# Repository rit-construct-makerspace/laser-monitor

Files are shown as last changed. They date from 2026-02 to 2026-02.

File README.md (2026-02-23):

# Laser Monitor 

This circuit will monitor a laser cutter's filter control and air input, and ensure both are operating properly when the laser is on. If not, warn the user.

## Setup
* Connect the fume extractor control line to the female DB9 of the laser monitor.
  * If using V1.0.**0** hardware, must invert the pinout with an adapter cable.
  * 5-1, 9-6, 4-2, 8-7, 3-3, 7-8, 2-4, 6-9, 1-5
* Connect the male DB9 on the laser monitor to the laser cutter's fume control output.
* Cut the air line to the laser cutter, and install the flex host T-joint.
* Connect 3mm ID tube to the air transducer on the PCB, and the other side to the T-joint.
* Connect 12v power supply.
* Connect laser monitor via USB to computer, open serial terminal with baud rate 115200.
* Send the following config commands;
  * Set the start delay with d [ms], i.e. "d 10000" for a 10-second startup
    * Make sure to set the same startup time in the Epilog laser
  * Set the air pressure threshold with a [val], i.e. "a 7000000"
    * Tip: use "c" to see the current air monitor reading to determine a threshold appropriate for your system.
  * Set the filter full warning with w [0/1], i..e "w 1" if you want to be warned when the filter is reporting full
    * This does not disable the fault response, just the low pressure filter warning.
  * You should be all set! Make sure to do tests on the system.

## Bill of Materials
* Assembled PCB (See Electronics Folder)
* 6x 3mm Plywood Laser Cut Case Parts (See Mechanical Folder)
* 12v >3A Barrel Jack Power Supply
* Andon Light Tower (12v) With Buzzer
  * Suggested that a blinking red light is used
  * Common anode or common cathode systems permitted, set control mode switch accordingly.
* DB9 Extension Cable (Connect Laser to Laser Monitor)
* Flex Hose T-Joint
* 3mm ID Flex Hose (OD sized to fit current system, 8mm normal)
* SparkFun 14 Segment Dispaly COM-16916 (Optional) + QWIIC to 2.54mm DuPont cable
* Threaded Rubber Magnet (1/4-20 thread)
* Hardware
  * 4x M2.5 25mm Standoffs
  * 4x M2.5 12mm Standoffs
  * 4x M2.5 6mm Spacers
  * 8x M2.5 Screw
  * 8x M2.5 Nut
  * 4x M5 Bolt
  * 4x M5 Nut

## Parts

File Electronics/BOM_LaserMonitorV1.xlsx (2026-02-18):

No. | Quantity | Comment | Designator | Footprint | Value | Manufacturer Part | Manufacturer | Supplier Part | Supplier
1 | 2 | 10uF | C1,C5 | C0603 | 10uF | CL10A106MA8NRNC | SAMSUNG(三星) | C96446 | LCSC
2 | 21 | 100nF | C2,C3,C4,C6,C7,C12,C13,C14,C15,C16,C17,C20,C21,C22,C23,C26,C27,C29,C30,C31,C32 | C0603 | 100nF | CC0603KRX7R9BB104 | YAGEO(国巨) | C14663 | LCSC
3 | 4 | 22uF | C8,C9,C10,C11 | C1206 | 22uF | CL31A226KAHNNNE | SAMSUNG(三星) | C12891 | LCSC
4 | 3 | 1uF | C18,C19,C28 | C0603 | 1uF | CL10A105KB8NNNC | SAMSUNG(三星) | C15849 | LCSC
5 | 2 | 15pF | C24,C25 | C0603 | 15pF | CL10C150JB8NNNC | SAMSUNG(三星) | C1644 | LCSC
6 | 1 | DR-9M | CN1 | DR9-TH_ZHOUR_DR-9P-R |  | DR-9M | ZHOURI(洲日) | C3020655 | LCSC
7 | 1 | DR-9F | CN2 | DR9-TH_ZHOUR_DR-9P-L |  | DR-9F | ZHOURI(洲日) | C3020657 | LCSC
8 | 1 | DB103-5.0-5P-BU-S | CN3 | CONN-TH_5P-P5.00_DB103-5.0-5P-BU-S |  | DB103-5.0-5P-BU-S | DORABO(地博电气) | C430589 | LCSC
9 | 1 | 921-111A1010D10200 | CN4 | USB-B_TH_USB-B-FEMALE-90 |  | 921-111A1010D10200 | 精拓金 | C46392 | LCSC
10 | 1 | DS1038-15FBNSiA74-0CC | CN5 | DSUB-TH_DS1038-15FBNSIA74-0CC |  | DS1038-15FBNSiA74-0CC | CONNFLY | C75754 | LCSC
11 | 5 | SS34 | D1,D2,D3,D4,D7 | SMA_L4.3-W2.6-LS5.2-RD |  | SS34 | MDD(辰达半导体) | C8678 | LCSC
12 | 4 | SRV05-4 | D5,D6,D8,D9 | SOT-23-6_L2.9-W1.6-P0.95-LS2.8-BL |  | SRV05-4 | TECH PUBLIC(台舟) | C558418 | LCSC
13 | 1 | DC-005-A250 | DC1 | DC-IN-TH_DC-005-A250 |  | DC-005-A250 | XUNPU(讯普) | C720558 | LCSC
14 | 4 | MF-NSMF050-2 | F1,F2,F3,F4 | F1206 |  | MF-NSMF050-2 | BOURNS | C75464 | LCSC
15 | 1 | HDR-M_2.54_1x4P | H1 | HDR-TH_4P-P2.54-V-M
16 | 1 | HDR-F_2.54_2x3 | H2 | HDR-TH_6P-P2.54-V-F-R2-C3-S2.54
17 | 1 | 10uH | L1 | L1206 | 10uH | CMI321609X100KT | FH(风华) | C1051 | LCSC
18 | 1 | KT-0603R | LED1 | LED0603-RD |  | KT-0603R | KENTO | C2286 | LCSC
19 | 1 | MMBT4403 | Q1 | SOT-23-3_L2.9-W1.3-P0.95-LS2.4-BR |  | MMBT4403 | R+O(宏嘉诚) | C20069140 | LCSC
20 | 1 | 20kΩ | R1 | R0603 | 20kΩ | 0603WAF2002T5E | UNI-ROYAL(厚声) | C4184 | LCSC
21 | 1 | 8.2kΩ | R2 | R0603 | 8.2kΩ | 0603WAF8201T5E | UNI-ROYAL(厚声) | C25981 | LCSC
22 | 2 | 100Ω | R3,R4 | R0603 | 100Ω | 0603WAF1000T5E | UNI-ROYAL(厚声) | C22775 | LCSC
23 | 14 | 390Ω | R5,R6,R8,R9,R11,R12,R14,R15,R17,R18,R19,R20,R29,R37 | R0805 | 390Ω | 0805W8F3900T5E | UNI-ROYAL(厚声) | C17655 | LCSC
24 | 13 | 10kΩ | R7,R10,R13,R16,R22,R23,R24,R25,R31,R32,R33,R34,R35 | R0603 | 10kΩ | 0603WAF1002T5E | UNI-ROYAL(厚声) | C25804 | LCSC
25 | 4 | 4.7kΩ | R21,R26,R27,R28 | R0603 | 4.7kΩ | 0603WAF4701T5E | UNI-ROYAL(厚声) | C23162 | LCSC
26 | 2 | 1kΩ | R30,R36 | R0603 | 1kΩ | 0603WAF1001T5E | UNI-ROYAL(厚声) | C21190 | LCSC
27 | 1 | SS-22F07-G100 | SW1 | SW-TH_6P-L16.5-W7.5-P4.0-LS2.6-TL |  | SS-22F07-G100 | G-Switch(品赞) | C5446810 | LCSC
28 | 1 | HX711 | U1 | SOP-16_L10.0-W3.9-P1.27-LS6.0-BL |  | HX711 | AVIA(海芯科技) | C6705483 | LCSC
29 | 1 | WF100SPZ 2BG D6 AT | U2 | DIP-6_L8.5-W8.5-P2.54-LS10.2-TL |  | WF100SPZ 2BG D6 AT | WF(伟烽) | C2886644 | LCSC
30 | 12 | AT172-CuH-S | U3,U4,U5,U6,U7,U8,U9,U10,U11,U12,U13,U14 | SOP-4_L4.6-W4.2-P2.54-LS7.1-BL |  | AT172-CuH-S | AOTE(奥特) | C20624244 | LCSC
31 | 4 | SN74LVC1T45DBVR | U15,U16,U17,U18 | SOT-23-6_L2.9-W1.6-P0.95-LS2.8-BR |  | SN74LVC1T45DBVR | TI(德州仪器) | C7843 | LCSC
32 | 2 | MX5052S | U19,U24 | SOP-8_L4.9-W3.9-P1.27-LS6.0-BL |  | MX5052S | Wuxi Maxinmicro(无锡明芯微) | C5875696 | LCSC
33 | 1 | DS18B20Z | U20 | SOP-8_L4.9-W3.9-P1.27-LS6.0-BL |  | DS18B20Z | UMW(友台半导体) | C695837 | LCSC
34 | 1 | L78M05ABDT-TR | U21 | TO-252-2_L6.5-W6.1-P4.58-LS10.0-TL |  | L78M05ABDT-TR | ST(意法半导体) | C58069 | LCSC
35 | 1 | ATMEGA328PB-AU | U22 | TQFP-32_L7.0-W7.0-P0.80-LS9.0-BL |  | ATMEGA328PB-AU | MICROCHIP(美国微芯) | C132230 | LCSC
36 | 1 | CH340C | U23 | SOP-16_L10.0-W3.9-P1.27-LS6.0-BL |  | CH340C | WCH(南京沁恒) | C7464026 | LCSC
37 | 1 | 16MHz | X1 | OSC-SMD_4P-L3.2-W2.5-BL | 16MHz | X322516MLB4SI | YXC(扬兴晶振) | C13738 | LCSC

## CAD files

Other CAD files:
Mechanical/Laser Monitor Assembly.f3z

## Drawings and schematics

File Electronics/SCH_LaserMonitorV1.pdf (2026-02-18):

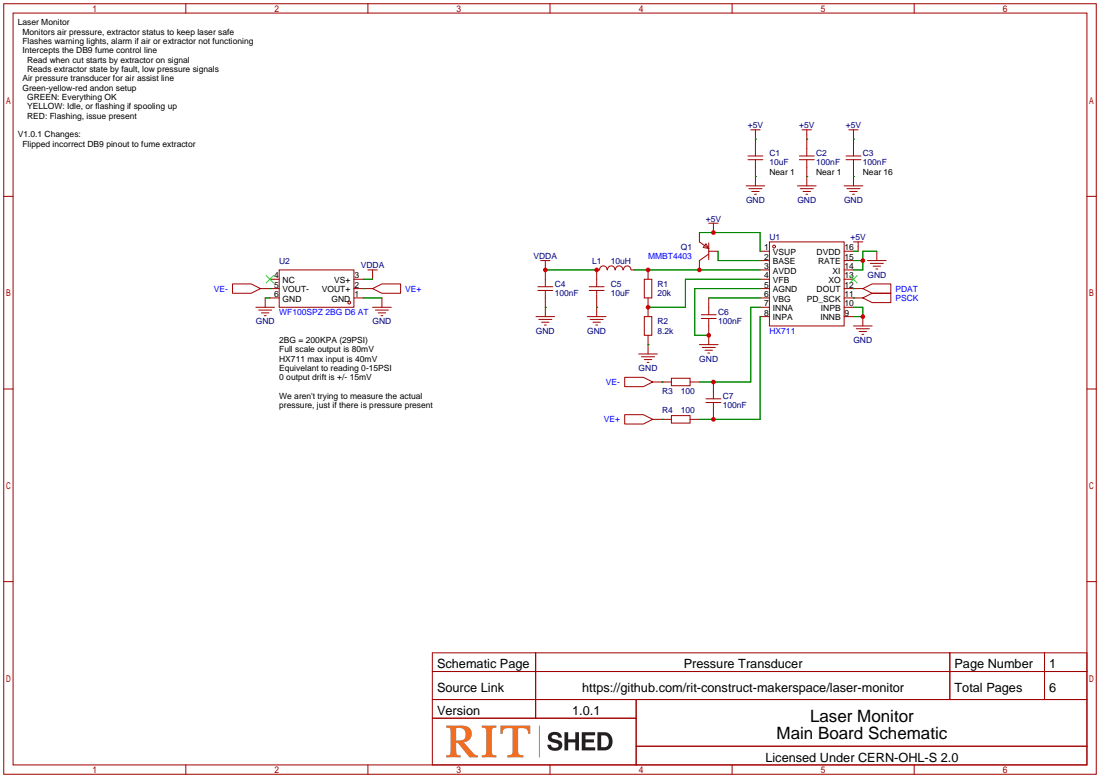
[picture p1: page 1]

Laser Monitor
Monitors air pressure, extractor status to keep laser safe
Flashes warning lights, alarm if air or extractor not functioning
Intercepts the DB9 fume control line
Read when cut starts by extractor on signal
Reads extractor state by fault, low pressure signals
Air pressure transducer for air assist line
Green-yellow-red andon setup
GREEN: Everything OK
YELLOW: Idle, or flashing if spooling up
RED: Flashing, issue present
V1.0.1 Changes:
Flipped incorrect DB9 pinout to fume extractor

INPB 10 PD_SCK 11 DOUT 12 XO 13 XI 14 RATE 15 DVDD 16

VOUT- 5
GND 6
WF100SPZ 2BG D6 AT
2BG = 200KPA (29PSI)
Full scale output is 80mV
HX711 max input is 40mV
Equivelant to reading 0-15PSI
0 output drift is +/- 15mV
We aren't trying to measure the actual
pressure, just if there is pressure present

Schematic Page | Pressure Transducer | Page Number | 1
Source Link | https://github.com/rit-construct-makerspace/laser-monitor | Total Pages | 6

Main Board Schematic

Licensed Under CERN-OHL-S 2.0

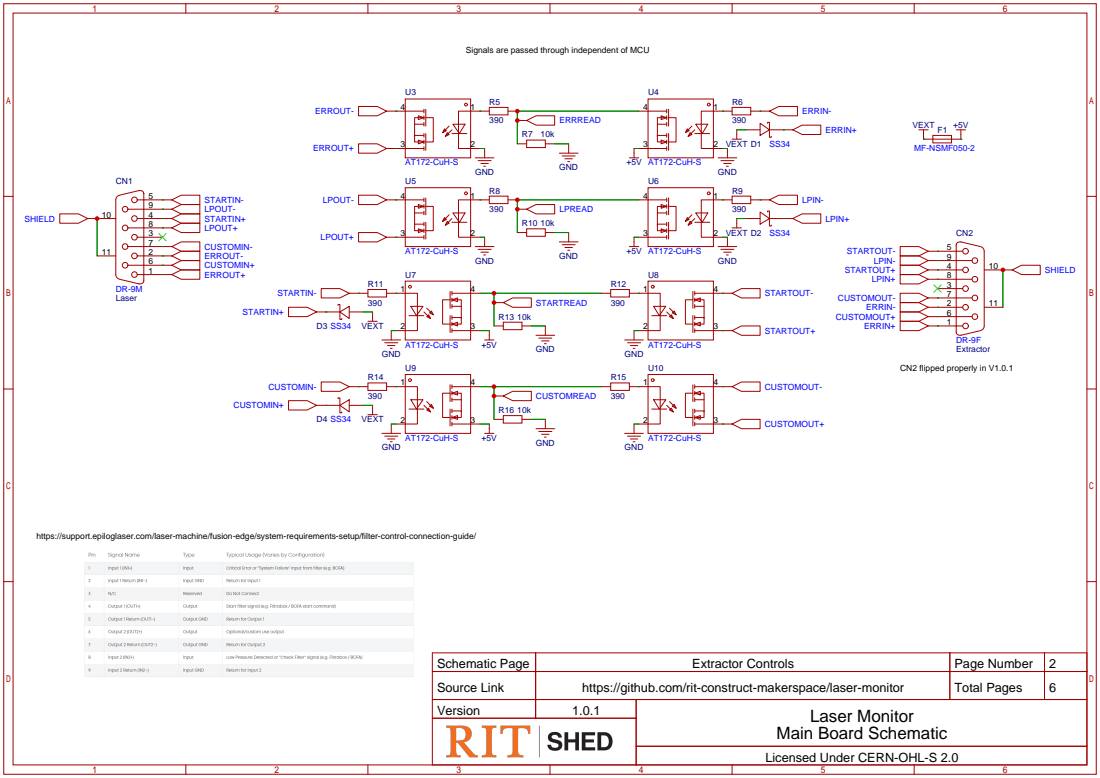
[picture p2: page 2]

Signals are passed through independent of MCU

https://support.epiloglaser.com/laser-machine/fusion-edge/system-requirements-setup/filter-control-connection-guide/

Schematic Page | Extractor Controls | Page Number | 2
Source Link | https://github.com/rit-construct-makerspace/laser-monitor | Total Pages | 6

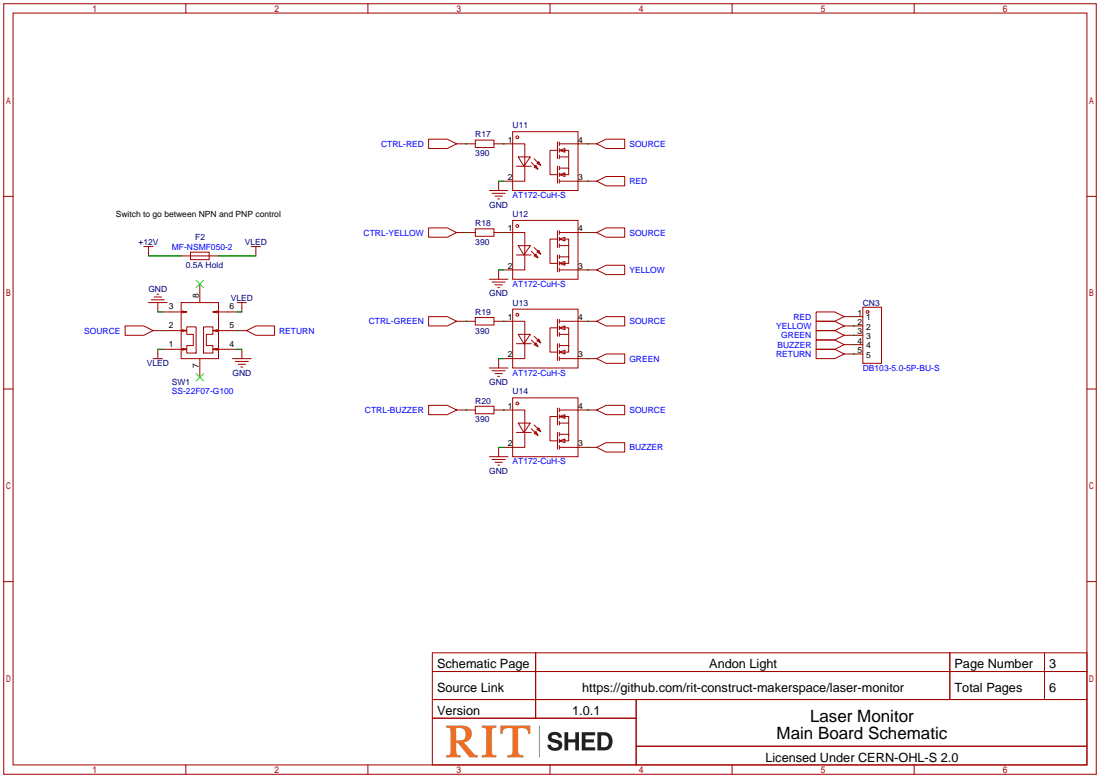
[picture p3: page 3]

Switch to go between NPN and PNP control

Schematic Page | Andon Light | Page Number | 3
Source Link | https://github.com/rit-construct-makerspace/laser-monitor | Total Pages | 6

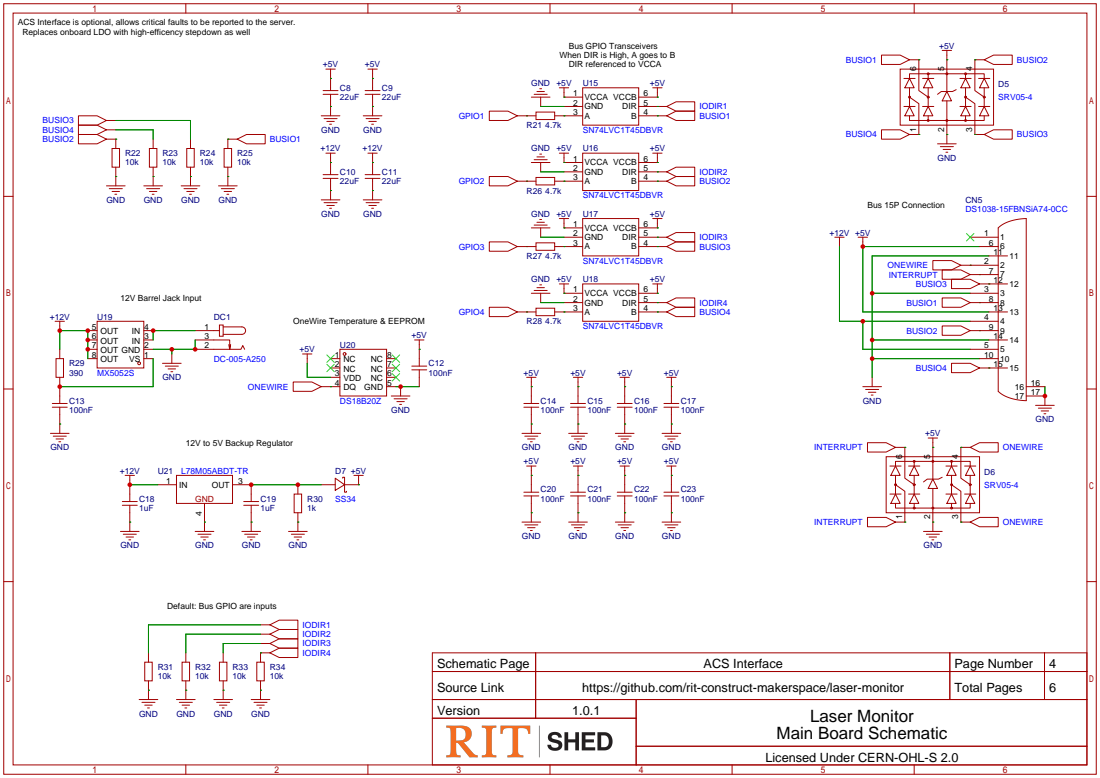
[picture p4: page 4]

ACS Interface is optional, allows critical faults to be reported to the server.
Replaces onboard LDO with high-efficency stepdown as well

Default: Bus GPIO are inputs

Schematic Page | ACS Interface | Page Number | 4
Source Link | https://github.com/rit-construct-makerspace/laser-monitor | Total Pages | 6

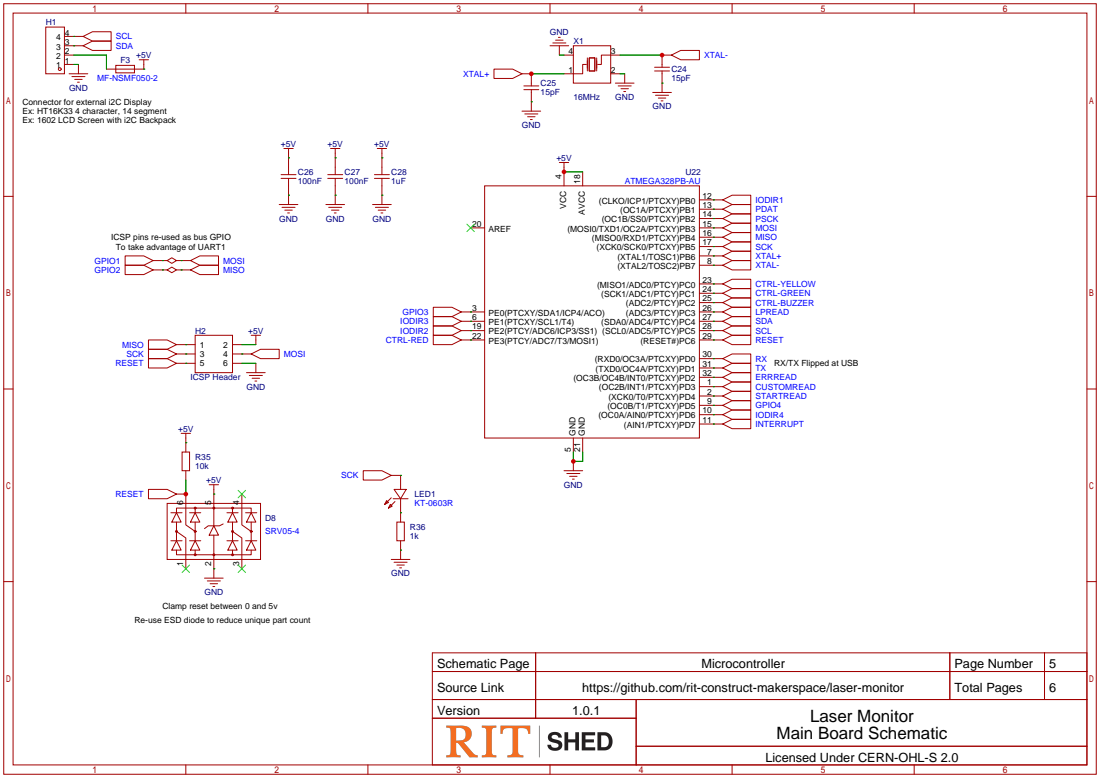
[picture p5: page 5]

Connector for external i2C Display
Ex: HT16K33 4 character, 14 segment
Ex: 1602 LCD Screen with i2C Backpack

ICSP pins re-used as bus GPIO
To take advantage of UART1
GPIO1
GPIO2

Clamp reset between 0 and 5v
Re-use ESD diode to reduce unique part count

Schematic Page | Microcontroller | Page Number | 5
Source Link | https://github.com/rit-construct-makerspace/laser-monitor | Total Pages | 6

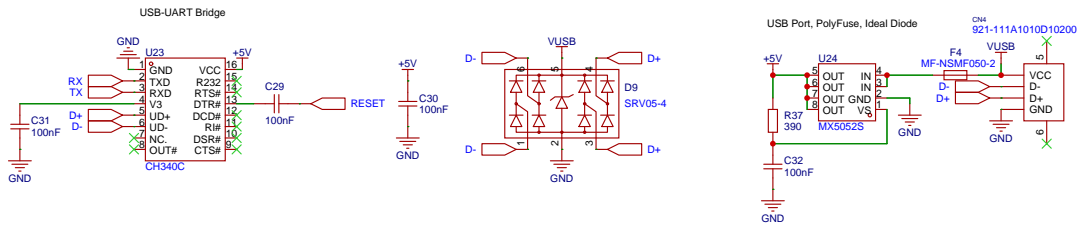
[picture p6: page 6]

USB Port, PolyFuse, Ideal Diode

DSR# 10 RI# 11 DCD# 12 DTR# 13 RTS# 14 R232 15 VCC 16

Schematic Page | USB-UART | Page Number | 6
Source Link | https://github.com/rit-construct-makerspace/laser-monitor | Total Pages | 6

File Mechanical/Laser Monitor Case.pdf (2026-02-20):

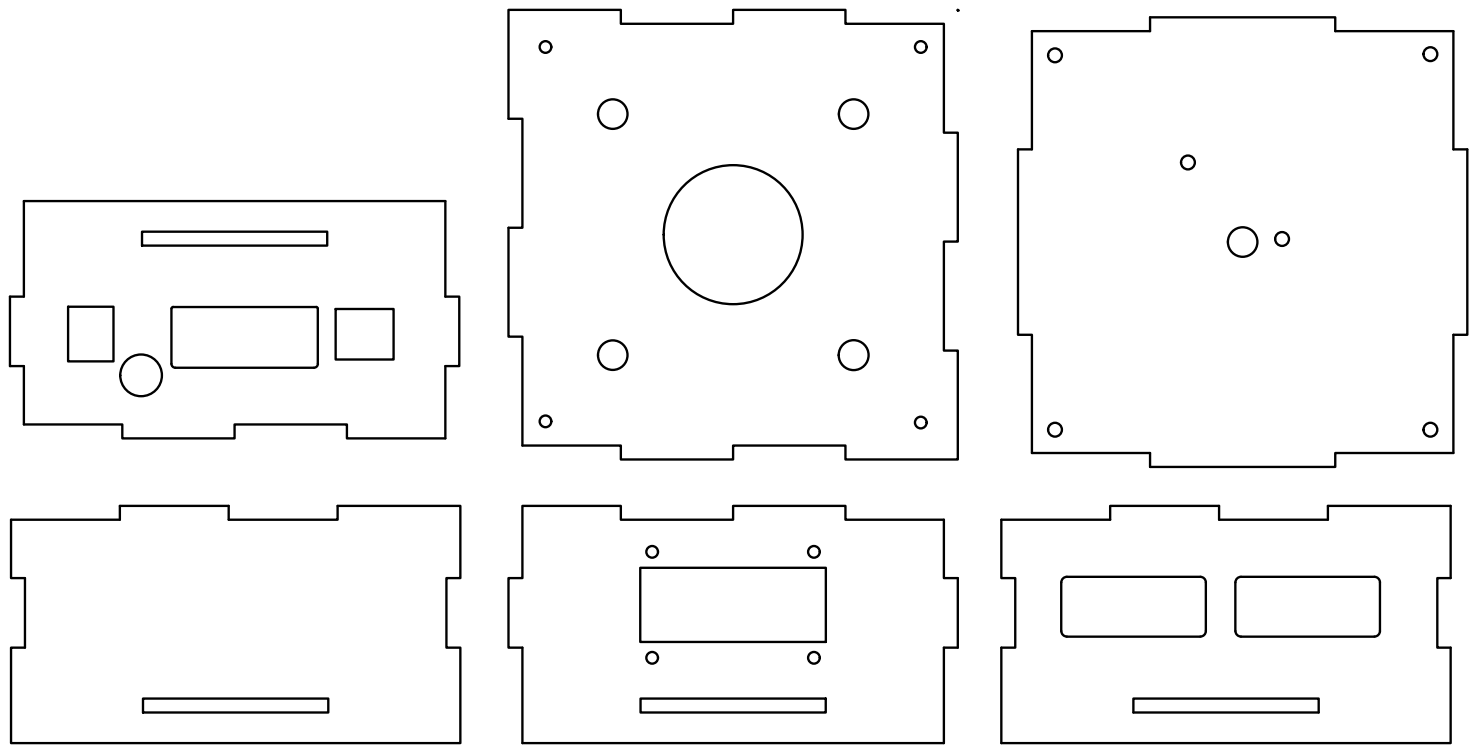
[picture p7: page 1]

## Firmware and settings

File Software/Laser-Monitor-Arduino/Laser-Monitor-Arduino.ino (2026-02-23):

// Laser Monitor 
// This circuit monitors air pressure and fume extractor status for a laser cutter.

#define VERSION "V1.0.0-A"
#define HWVer "V1.0.0"

#include <avr/wdt.h>
#include <Wire.h>
#include <EEPROM.h>
#include "HX711.h"
#include <SparkFun_Alphanumeric_Display.h>

// Objects
HX711 air;
HT16K33 display;

// Constants (Pins and Memory Offsets)
const byte PIN_AIR_DATA      = PIN_PB1;
const byte PIN_AIR_CLOCK     = PIN_PB2;
const byte PIN_YELLOW        = PIN_PC0;
const byte PIN_GREEN         = PIN_PC1;
const byte PIN_BUZZER        = PIN_PC2;
const byte PIN_RED           = PIN_PE3;
const byte PIN_START_READ    = PIN_PD4;
const byte PIN_ERROR_READ    = PIN_PD2;
const byte PIN_LP_READ       = PIN_PC3;
const byte PIN_ACS_INTERRUPT = PIN_PD7;

const int ADDR_AIR_THRESHOLD = 0;
const int ADDR_START_DELAY   = 10;
const int ADDR_BRIGHTNESS    = 20;
const int ADDR_WARNING       = 30;

// Variables
byte brightness           = 0;
long airThreshold         = 0;
long startDelay           = 0;
unsigned long flashTimer  = 0;
bool flashState           = false;
bool filterWarning        = false;

// Function Prototypes
void runMonitor();
void printCurrentState();
void enterFaultState();
void setAndon(bool red, bool yellow, bool green, bool buzzer);
void setInterrupt(bool active);
bool isAirPressureOk();

void setup() {
  Serial.begin(115200);

  // Initialize Sensors and Displays
  air.begin(PIN_AIR_DATA, PIN_AIR_CLOCK);
  Wire.begin();
  display.begin();

  // Retrieve Settings from EEPROM
  EEPROM.get(ADDR_AIR_THRESHOLD, airThreshold);
  EEPROM.get(ADDR_START_DELAY, startDelay);
  EEPROM.get(ADDR_BRIGHTNESS, brightness);
  EEPROM.get(ADDR_WARNING, filterWarning);

  display.setBrightness(brightness);

  // Set Pin Modes
  pinMode(PIN_YELLOW, OUTPUT);
  pinMode(PIN_GREEN, OUTPUT);
  pinMode(PIN_RED, OUTPUT);
  pinMode(PIN_BUZZER, OUTPUT);
  pinMode(PIN_START_READ, INPUT);
  pinMode(PIN_ERROR_READ, INPUT);
  pinMode(PIN_LP_READ, INPUT);
}

void loop() {

  // Idle State display/lights
  if (digitalRead(PIN_START_READ)) {
    runMonitor();
  }
  
  display.print("STBY");
  setAndon(false, true, false, false);

  // Serial Command Handling
  if (Serial.available() >= 1) {
    String incoming = Serial.readString();
    incoming.trim();
    char command = incoming.charAt(0);

    if (command == 'c') {
      printCurrentState();
    } 
    else if (command == 'b') {
      incoming.remove(0, 2);
      int val = incoming.toInt();
      if (val <= 15) {
        brightness = val;
        EEPROM.put(ADDR_BRIGHTNESS, brightness);
        display.setBrightness(brightness);
      } else {
        Serial.println(F("ERROR: Brightness must be 0-15"));
      }
    } 
    else if (command == 'd') {
      incoming.remove(0, 2);
      startDelay = incoming.toInt();
      EEPROM.put(ADDR_START_DELAY, startDelay);
      Serial.print(F("Delay set to: "));
      Serial.print(startDelay);
      Serial.print(F(" milliseconds. ("));
      float airSeconds = startDelay / 1000.0;
      Serial.print(airSeconds);
      Serial.println(F(" seconds)."));
    } 
    else if (command == 'a') {
      incoming.remove(0, 2);
      airThreshold = incoming.toInt();
      EEPROM.put(ADDR_AIR_THRESHOLD, airThreshold);
      Serial.print(F("Air Threshold Set to: "));
      Serial.println(airThreshold);
    } 
    else if (command == 'v' || command == 'i'){
      Serial.println(F("Laser Monitor"));
      Serial.println(F("Developed by RIT SHED Makerspace"));
      Serial.println(F("make.rit.edu"));
      Serial.println(F("Licensed: CERN-OHL-S 2.0"));
      Serial.println(F("Source: https://github.com/rit-construct-makerspace/laser-monitor"));
      Serial.print(F("Hardware Version: ")); Serial.println(HWVer);
      Serial.print(F("Software Version: ")); Serial.println(VERSION);
    }
    else if (command == 'w'){
      incoming.remove(0, 2);
      filterWarning = incoming.toInt();
      EEPROM.put(ADDR_WARNING, filterWarning);
      if(filterWarning){
        Serial.println(F("Filter full warning enabled."));
      } else{
        Serial.println("Filter full warning disabled.");
      }
    }
    else {
      Serial.println(F("Commands: c (status), d [ms] (delay), a [val] (threshold), b [0-15] (bright), w [0/1] (filter warning), v (version), i (info)"));
    }
  }

  // Safety Reset if millis overflow is approaching (approx 34 days)
  if (millis() >= 3000000000) { 
    wdt_enable(WDTO_2S);
    while(1); 
  }

  delay(100);
}

void runMonitor() {
  unsigned long startTime = millis();
  bool blinking = false;
  bool FirstSerial = 0;
  
  while (digitalRead(PIN_START_READ)) {
    // 1. Determine State
    bool isStarting = (millis() - startTime < (unsigned long)startDelay);

    // 2. Serial Passthrough
    if (Serial.available()) {
      while(Serial.available()) Serial.read();
      if(!FirstSerial){
        FirstSerial = 1;
        Serial.println(F("Warning: while the laser is operating, all USB commands ignored except current state."));
      }
      printCurrentState();
    }

    // 3. Logic Branching
    if (isStarting) {
      display.print("WAIT");
      blinking = true;
    } 
    else {
      // Monitor Critical Faults
      if (!digitalRead(PIN_ERROR_READ)) {
        display.print("FUME");
        Serial.println(F("FAULT: Fume Extractor Offline!"));
        enterFaultState();
        break; 
      }

      if (!isAirPressureOk()) {
        display.print("AIR ");
        Serial.println(F("FAULT: Air Pressure Below Limit!"));
        enterFaultState();
        break;
      }

      // Check Non-Critical Warnings
      if (!digitalRead(PIN_LP_READ) && filterWarning) {
        display.print("FULL");
        blinking = true;
        Serial.println(F("WARNING: Low Pressure (Check Filter)"));
      } else {
        display.print("GOOD");
        blinking = false;
        setAndon(false, false, true, false);
      }
    }

    // 4. Handle Blinking Logic
    if (blinking) {
      if (millis() >= flashTimer) {
        flashTimer = millis() + 500;
        flashState = !flashState;
        setAndon(false, flashState, false, false);
      }
    }
  }
}

void printCurrentState() {
  Serial.println(F("\n--- System State ---"));
  Serial.print(F("Air Pressure: ")); Serial.println(air.read_average(10));
  Serial.print(F("Threshold:    ")); Serial.println(airThreshold);
  Serial.print(F("Laser Status: ")); Serial.println(digitalRead(PIN_START_READ) ? "RUNNING" : "IDLE");
  Serial.print(F("Fume Error:   ")); Serial.println(digitalRead(PIN_ERROR_READ) ? "OK" : "ERROR");
}

void enterFaultState() {
  printCurrentState();
  while (digitalRead(PIN_START_READ)) {
    setInterrupt(true);
    setAndon(true, false, false, true); // Red + Buzzer
  }
  setInterrupt(false);
}

void setAndon(bool red, bool yellow, bool green, bool buzzer) {
  digitalWrite(PIN_RED, red);
  digitalWrite(PIN_YELLOW, yellow);
  digitalWrite(PIN_GREEN, green);
  digitalWrite(PIN_BUZZER, buzzer);
}

void setInterrupt(bool active) {
  digitalWrite(PIN_ACS_INTERRUPT, LOW);
  if (active) {
    pinMode(PIN_ACS_INTERRUPT, OUTPUT);
  } else {
    pinMode(PIN_ACS_INTERRUPT, INPUT);
  }
}

bool isAirPressureOk() {
  return (air.read_average(10) > airThreshold);
}

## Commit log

2026-01-27 Updated for export
    [BOM_LaserMonitorV1.xlsx, PickAndPlace_LaserMonitorV1.xlsx]
2026-02-13 Laser Monitor Code
2026-02-18 V1.0.1 Outjob
    [BOM_LaserMonitorV1.xlsx, PickAndPlace_LaserMonitorV1.xlsx]
2026-02-20 Added mechanical design
    [Laser Monitor Assembly.f3z]
2026-02-20 Update README with Bill of Materials section
    Added a Bill of Materials section detailing components needed for the laser monitor project.
2026-02-20 Add 3mm ID flex hose to the parts list
2026-02-23 Update README with configuration commands
    Added configuration commands for laser cutter setup.
